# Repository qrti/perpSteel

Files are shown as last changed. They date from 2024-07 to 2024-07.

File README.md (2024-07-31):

# **Perpetual Steel Ball Track**

### As perpetual as the laws of physics of this universe allow
<br>

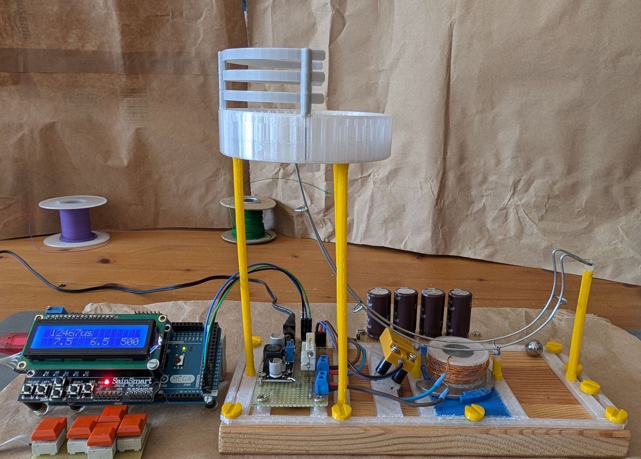
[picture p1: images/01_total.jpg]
<br>

YouTube Video  
https://www.youtube.com/watch?v=C1I4kvoMqeI

[**-> views**](#views)  
[**-> source**](source)  
<br>

## Background
The idea for building this device came to me while looking at a commercially available version. It was a long journey with much trial and error before the replica finally worked. The track had to be bent from steel wire, parts for the frame, collecting bowl, and supports had to be made with the 3D printer, the electromagnet had to be wound, and the electronics and software had to be developed
<br>

## Build
The building instructions for this project are not complete, they are only intended as an aid for a replica  
[**-> 3D-Printed Parts**](stl)

**Inner and Outer Track Template**  
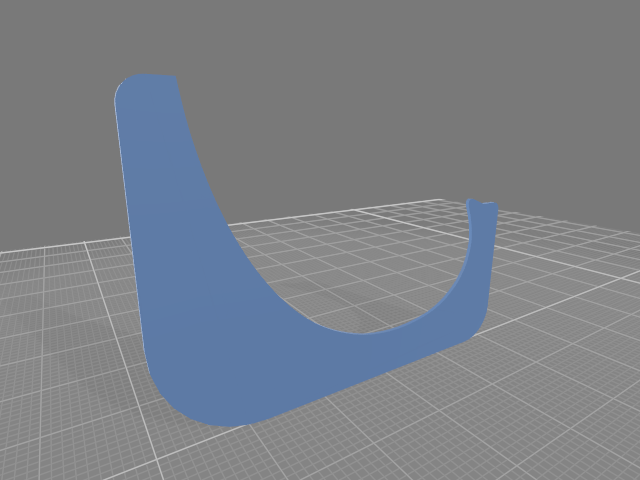
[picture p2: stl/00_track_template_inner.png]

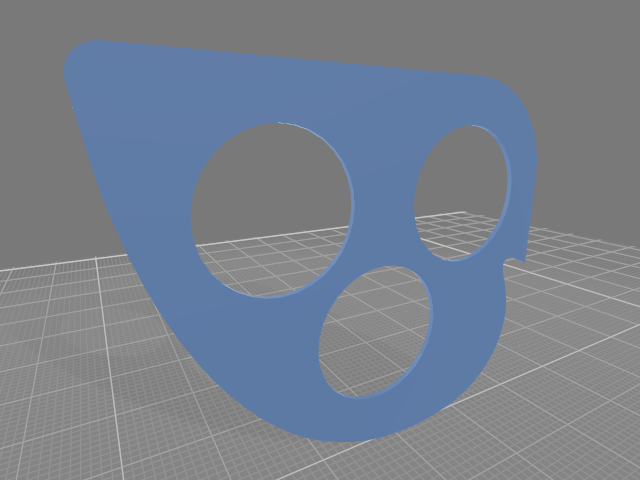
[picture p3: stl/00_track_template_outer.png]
  
The track was bent from 1.5 mm galvanized iron wire, as this is easy to work with and solder,  
the templates are meant to make bending easier  
<br>

**Cup and Cup Guide**  
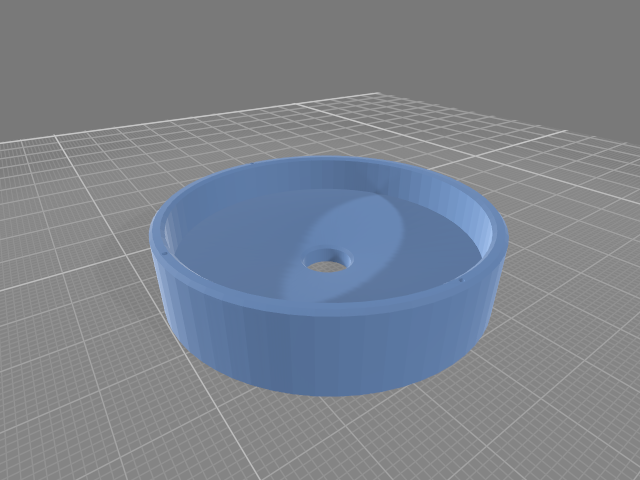
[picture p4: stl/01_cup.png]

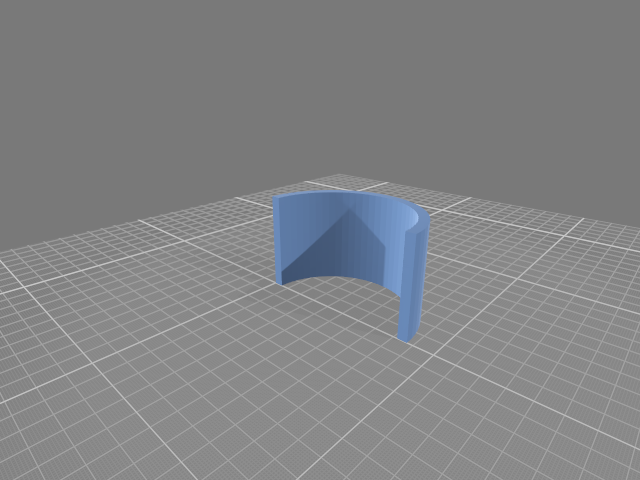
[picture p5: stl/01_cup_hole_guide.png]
  
To prevent the steel ball from derailing a guide is glued to the outlet of the cup hole  
<br>

**Rail Type 1 and 2**  
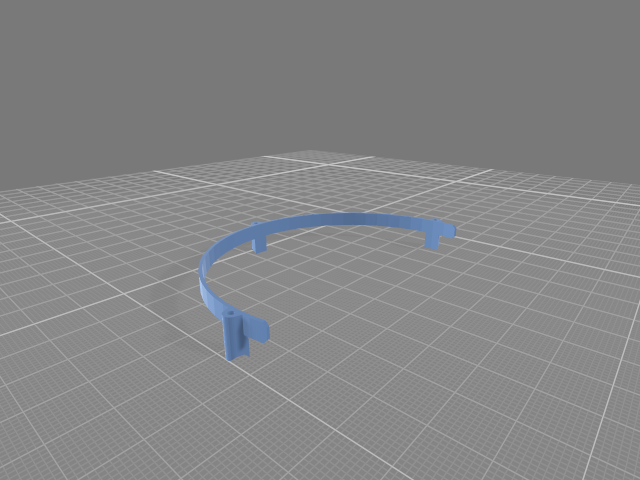
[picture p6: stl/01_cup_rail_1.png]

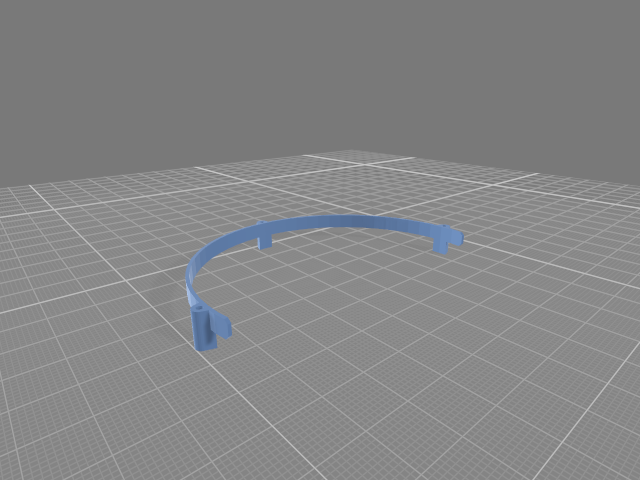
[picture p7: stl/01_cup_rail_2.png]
  
Type 1 is fixed to the rim of the cup, two pieces of type 2 are mounted above,  
to connect cup and rails sticks of steel wire are put in the provided holes  
<br>

**Electro Magnet Bobbin and Magnetic Field Guide Template**  
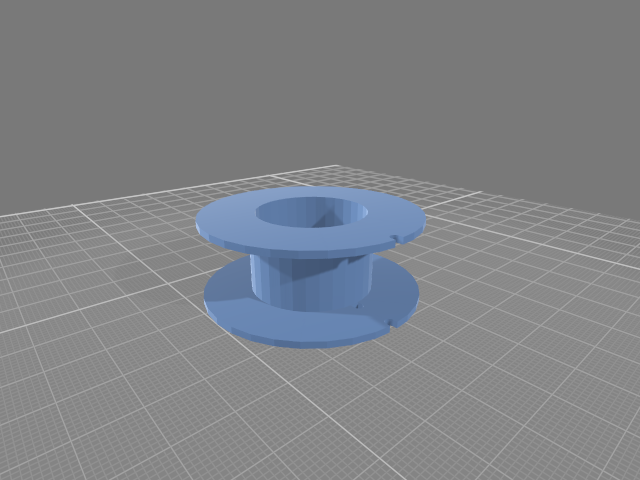
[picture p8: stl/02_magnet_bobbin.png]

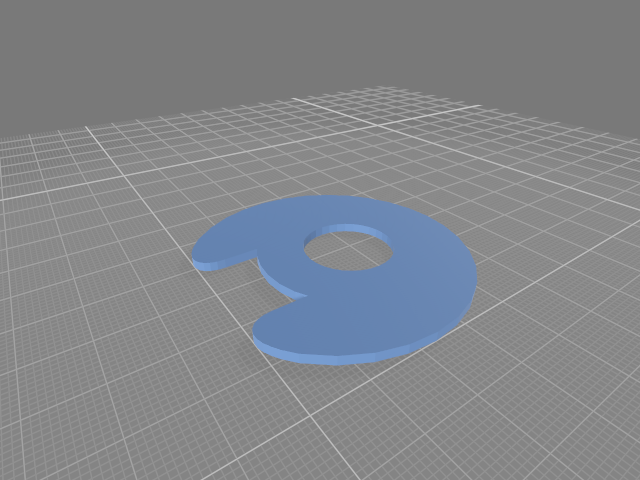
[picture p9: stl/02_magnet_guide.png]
  
The bobbin is completely wound with 0.8 mm enameled copper wire,  
the soft iron core has a diameter of 20 mm and is 16 mm long,  
the magnetic field guide is intended to center the steel ball in front of the magnet,  
it is made from 3 mm thick sheet iron, only the outlines of the template are relevant,  
so the hole in the template is not transferred to the sheet  
(the field guide can possibly be omitted)  
<br>

**Inductive Proximity Sensor and Arduino**  
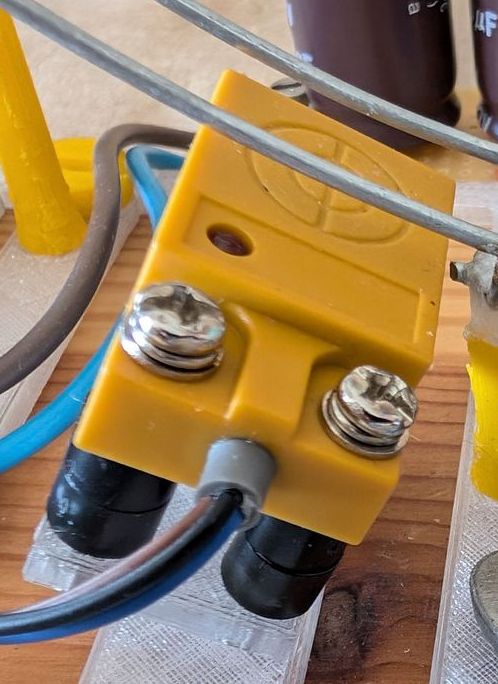
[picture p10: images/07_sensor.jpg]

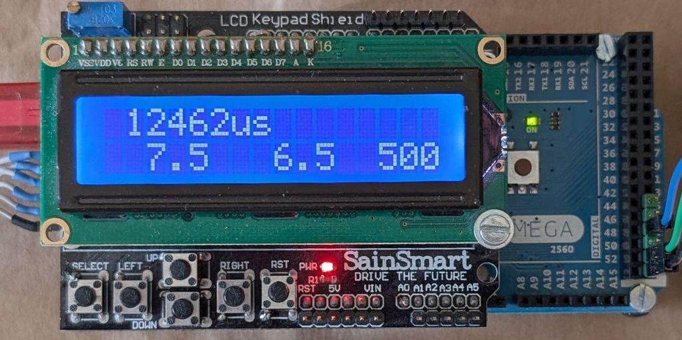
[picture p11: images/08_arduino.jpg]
  
This kind of sensor is normally used in 3D-Printers, see the schematic for more details,  
an Arduino Mega 2560 handles timing and delays for sensor and magnet,  
the LCD shows current settings, the keys allow timing changes  
<br>

## Schematic
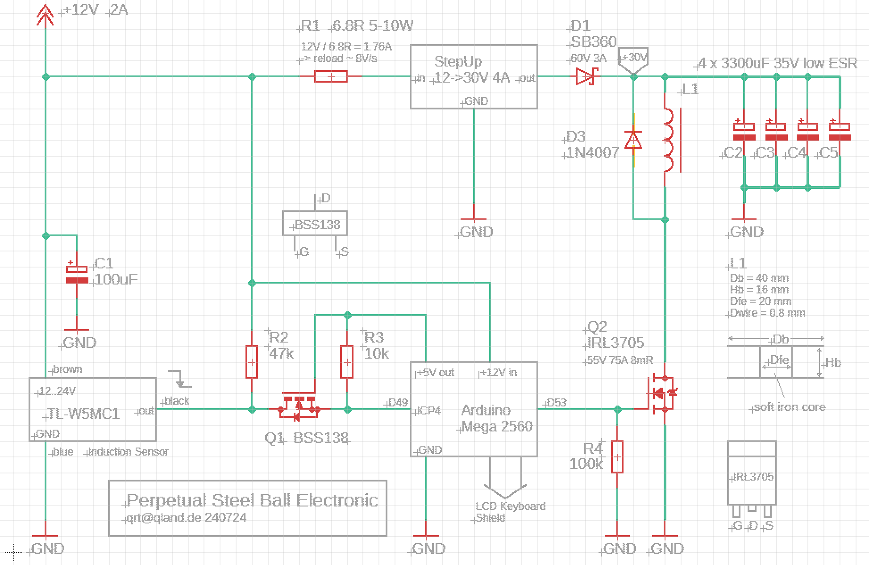
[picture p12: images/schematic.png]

<br>

## Operation
**Right Key**  
press about 1.5 s to enter or exit time and delay settings

**Select Key**  
change values in 100 / 500 / 1000 ms steps

**Left Key - / Right Key +**  
sensor OFF -> magnet ON delay

**Down Key - / Up Key +**  
magnet ON time  

(timing is saved to EEPROM after changes)

**Display**  
*Line 1*  
status or averaged sensor ON to OFF time in us

*Line 2*  
sensor OFF -> magnet ON delay in ms  
magnet ON time in ms  
change value in ms

**Calculation**  
sensor ON to OFF time is measured in TIMER4_CAPT and used as reciprocal relative speed (Vr)  
Vr is averaged and weighted, it influences the sensor OFF -> magnet ON delay
<br>

<br>
<br>

**Inspired by**  
https://www.youtube.com/watch?v=r_LG8FDt51U&t

**How to make a Steel Marble Track**  
https://www.youtube.com/watch?v=kPguktA674w

**Code Edited and Developed with**  
https://code.visualstudio.com/  
https://platformio.org/

<br>

---

<br>

## Views

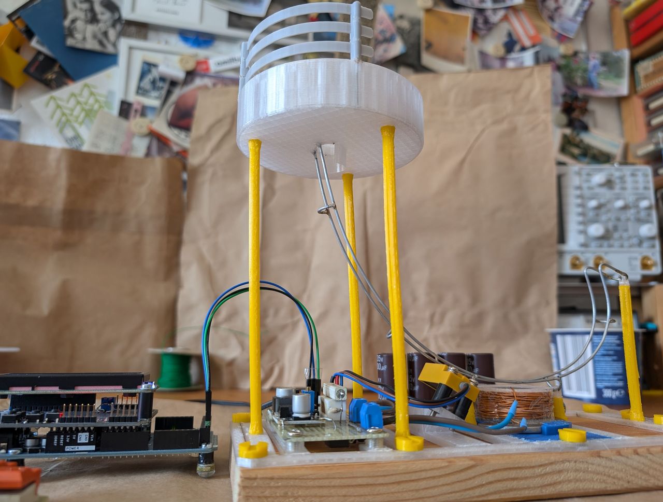
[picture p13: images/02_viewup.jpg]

<br>
<br>

Stepup Electronic and Capacitor Charge Resistors  
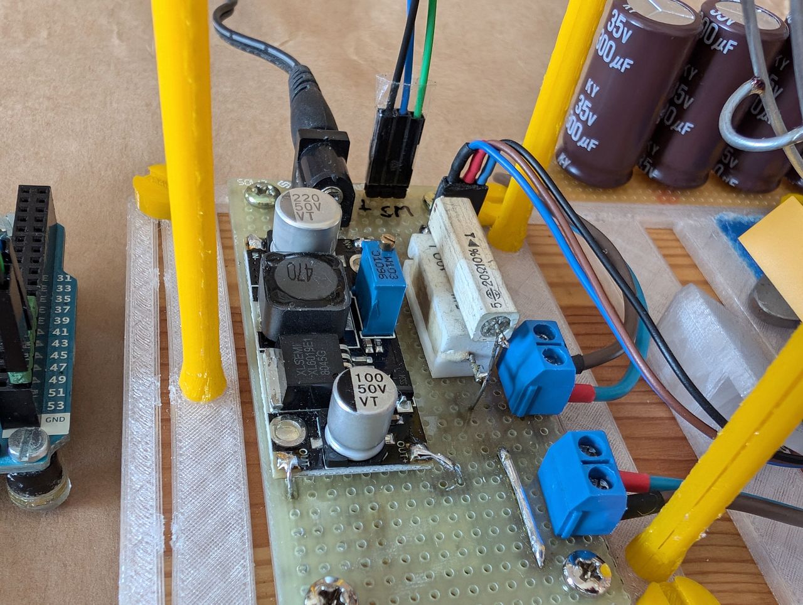
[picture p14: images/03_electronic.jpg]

<br>
<br>

Low ESR Capacitors 4 x 3300uF 35V  
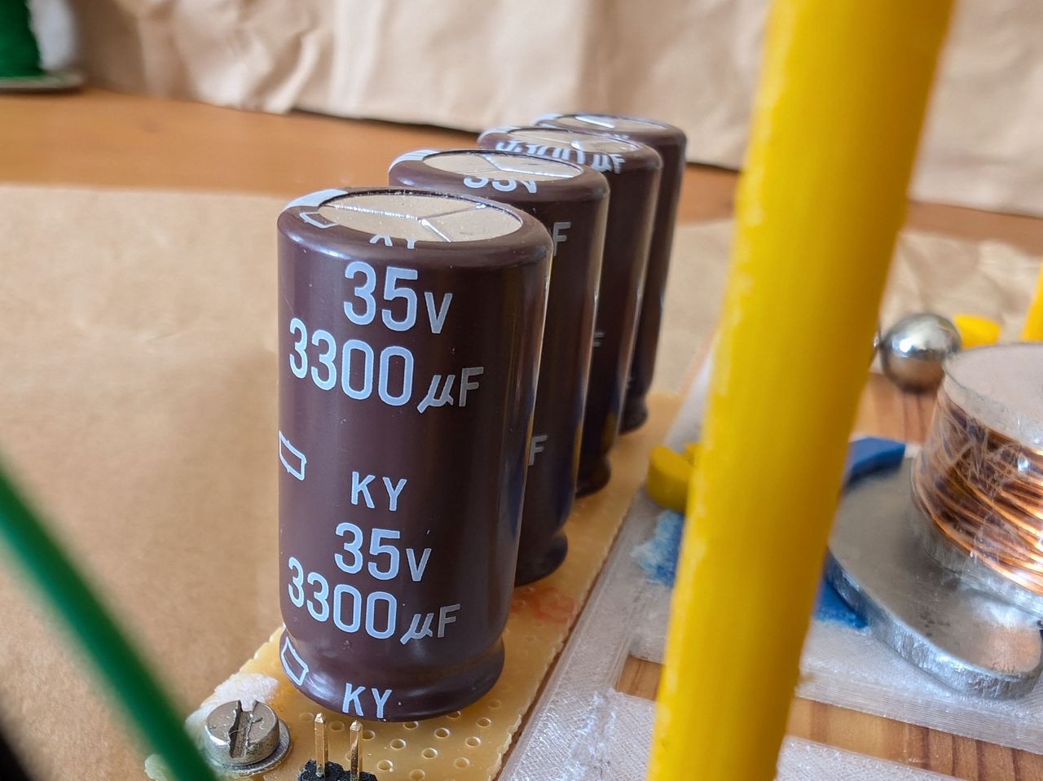
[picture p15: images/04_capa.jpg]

<br>
<br>

Inductive Proximity Sensor and Electro Magnet on Top of Magnetic Field Guide  
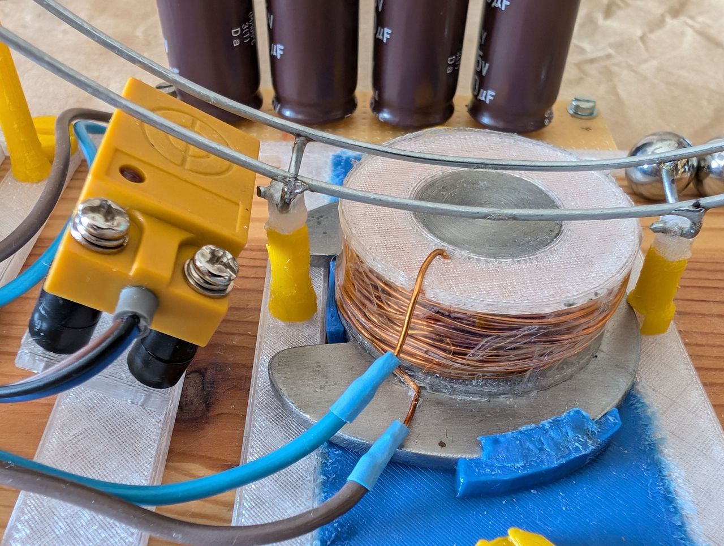
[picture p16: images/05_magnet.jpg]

<br>
<br>

Arduino Mega 2560 with LCD and Key Shield  
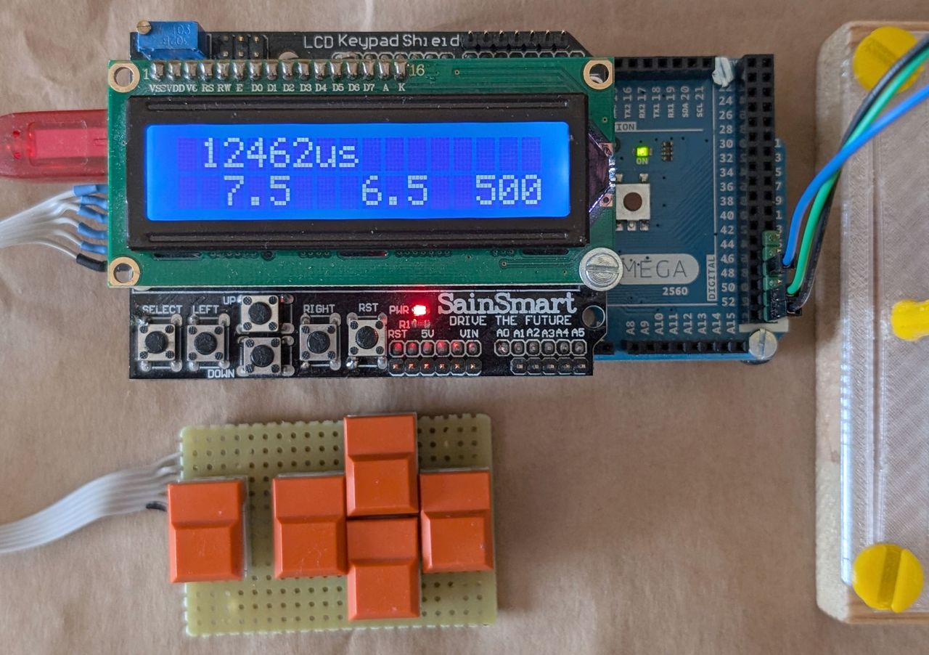
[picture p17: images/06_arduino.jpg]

<br>
<br>

<br>
<br>

---

[qrt@qland.de](mailto:qrt@qland.de) 240731

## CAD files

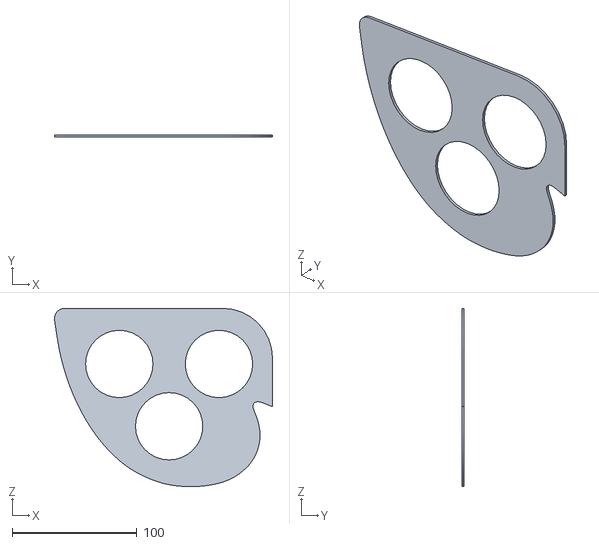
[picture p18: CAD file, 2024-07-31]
stl/00_track_template_outer.stl
174.9 x 2.00 x 143.2

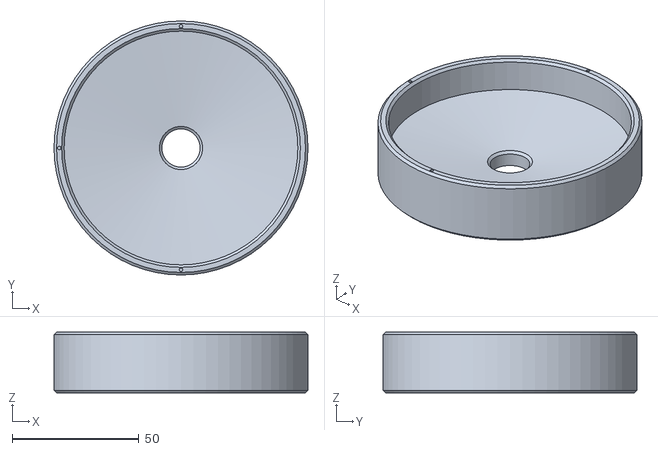
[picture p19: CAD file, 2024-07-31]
stl/01_cup.stl
100.0 x 100.0 x 24.0

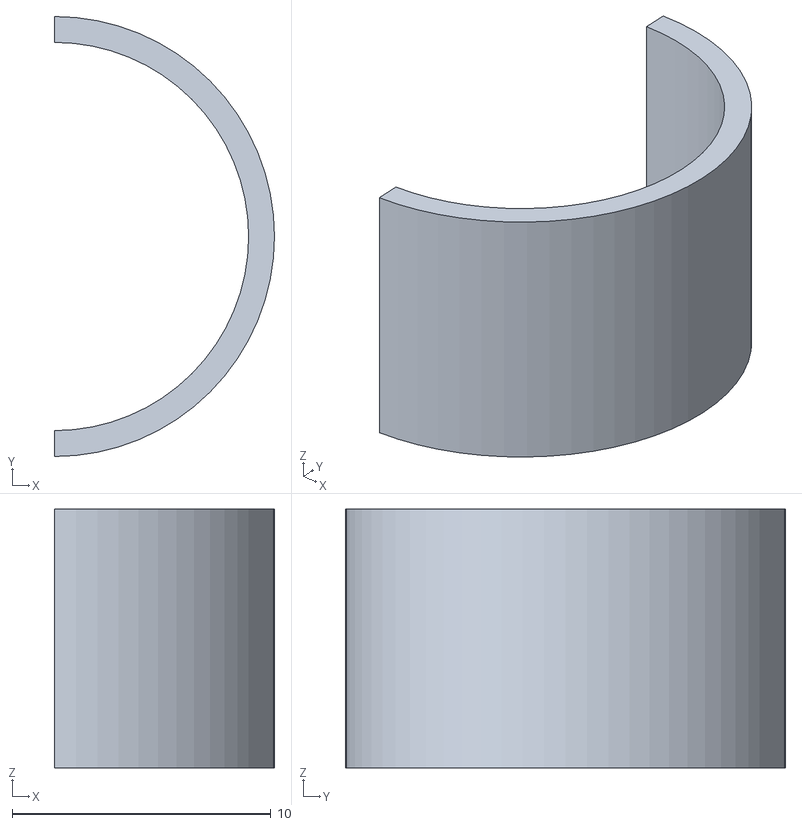
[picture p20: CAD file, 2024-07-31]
stl/01_cup_hole_guide.stl
8.50 x 17.0 x 10.0

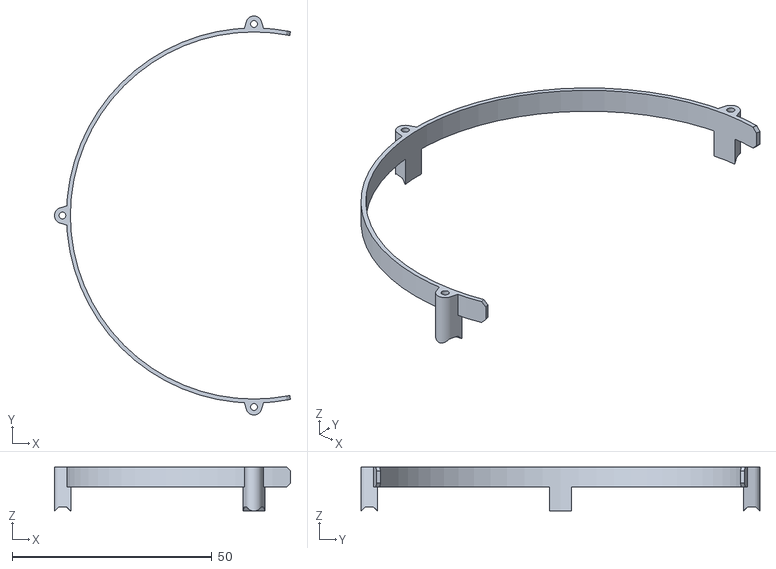
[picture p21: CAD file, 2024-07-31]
stl/01_cup_rail_1.stl
59.2 x 100.0 x 11.0

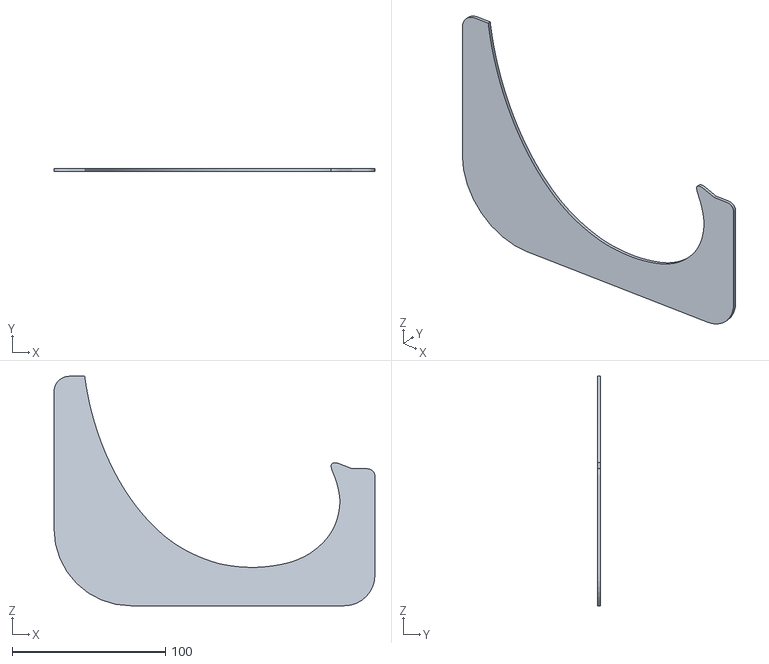
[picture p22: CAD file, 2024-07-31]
stl/00_track_template_inner.stl
209.3 x 2.00 x 149.7

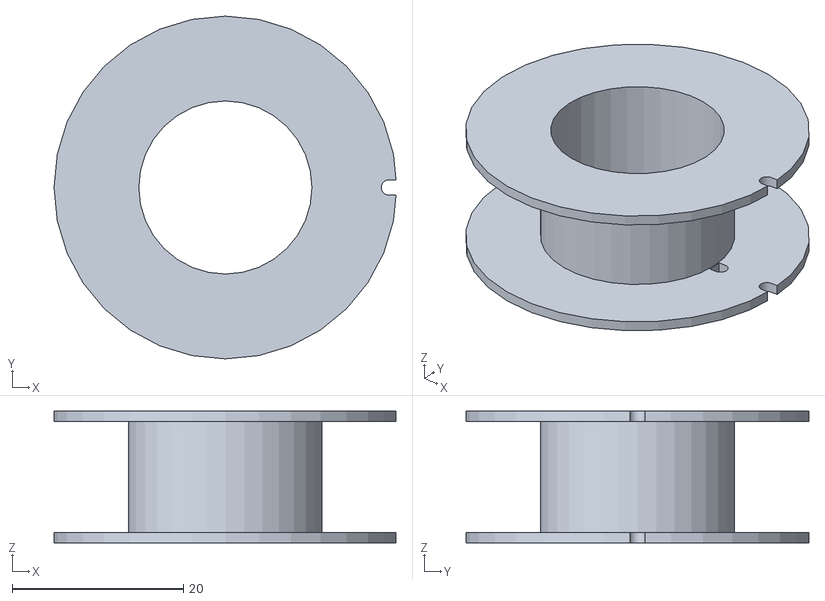
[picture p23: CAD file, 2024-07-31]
stl/02_magnet_bobbin.stl
39.9 x 40.0 x 15.4

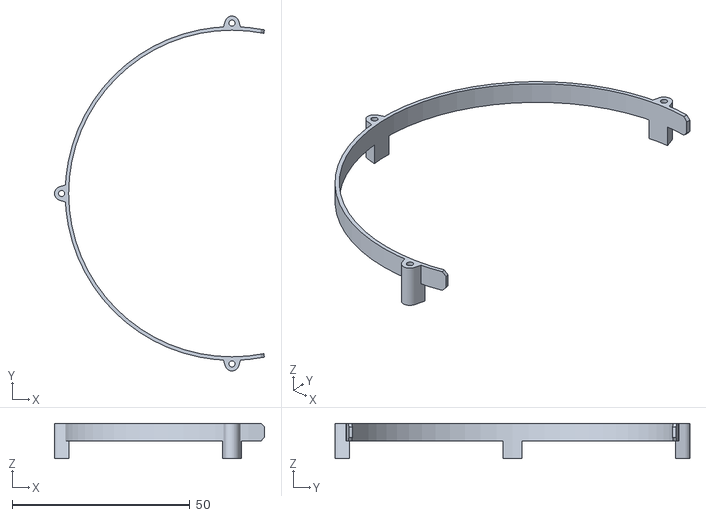
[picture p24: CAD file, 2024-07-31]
stl/01_cup_rail_2.stl
59.2 x 100.0 x 10.0

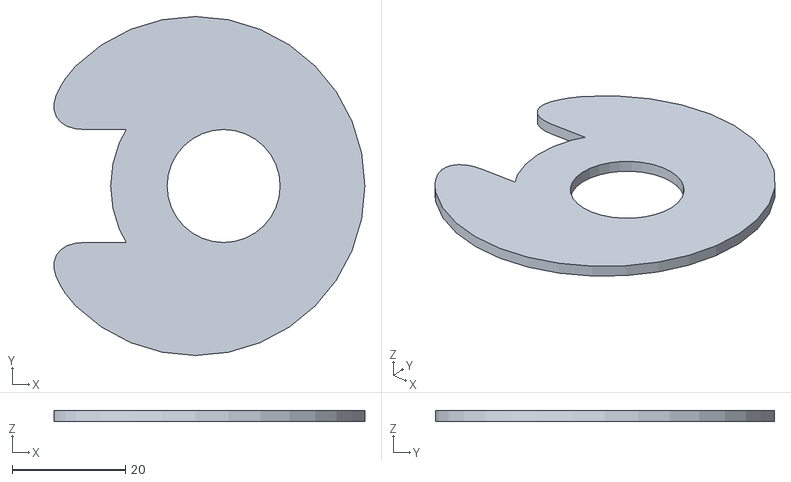
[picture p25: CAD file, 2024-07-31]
stl/02_magnet_guide.stl
55.0 x 60.0 x 2.00

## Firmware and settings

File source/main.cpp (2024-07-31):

// perpSteel V0.4, qrt@qland.de 240731

// KEY_RIGHT 
// press > 1.5 s to enter or exit time and delay settings
//
// KEY_SELECT
// change values in 100..500..1000 ms steps
//
// KEY_LEFT - / KEY_RIGHT +
// delay sensor OFF -> magnet ON
// 
// KEY_DOWN - / KEY_UP +
// magnet ON time
//
// the timing is saved to EEPROM after changes

// display
// line 1: status
//      2: sensor OFF -> magnet ON delay in ms, magnet ON time in ms, change value in ms

// calculation
// sensor ON to OFF time is measured in TIMER4_CAPT and used as reciprocal relative speed (Vr)
// Vr is averaged and weighted, it influences the sensor OFF -> magnet ON delay

// possible ICP pins on Arduino Mega 2560
// PIN      PORT    ICP     DIGITAL PIN     TIMER
// 35	    PL0     4       49              4
// 36	    PL1     5	    48              5

#include <Arduino.h>
#include <LiquidCrystal.h>
#include <EEPROM.h>
#include "LCDKeypadDA.h"

// default values for this machine, might be different for other machines
#define DEFAULT_TDELAY       6800               // sensor OUT -> magent ON delay    in us   
#define DEFAULT_TMAGPO       6000               // magnet ON time
#define DEFAULT_TNAVG       11000               // sensor ON to OFF time (Vr)

#define EESIG          0x18ab11cd               // EEPROM unique ID   

void changePars();

void showTiming();
void saveTiming();
void loadTiming();

void init_tmr4();

LiquidCrystal lcd(8, 9, 4, 5, 6, 7);
LCDKeypad keypad;

const int PIN_LED = 13;                         // LED
const int PIN_KEY_IRQ = 2;                      // IRQ0 for keys

const int PIN_INDUCT_SENSE = 49;                // ICP 4, TIMER 4
const int PIN_MAGPOW = 53;                      // magnet power 

#define ON      HIGH
#define OFF     LOW

volatile int32_t tdelay, tmagpo, dt;           // in us
uint32_t tdelayC;

volatile int32_t tsense;
volatile uint8_t f_capture = 0;                // flag

char buf[32];
int32_t tnSum, tnAvg, tnAvc=16;

// - - - - - - - - - - - - - - - - - - - - - - - - - - - - - - - - - - - - - - -

void setup()
{
    lcd.begin(16, 2);   
    lcd.clear();

    lcd.setCursor(0, 0);
    lcd.print("qrt 240731");

    pinMode(PIN_LED, OUTPUT);
    digitalWrite(PIN_LED, OFF);

    pinMode(PIN_INDUCT_SENSE, INPUT);

    pinMode(PIN_MAGPOW, OUTPUT);
    digitalWrite(PIN_MAGPOW, OFF);

    pinMode(A0, INPUT);

    loadTiming();

    delay(1000);
    lcd.clear();
    showTiming();

    init_tmr4();    
}

// - - - - - - - - - - - - - - - - - - - - - - - - - - - - - - - - - - - - - - -

uint32_t tmD, tmM;

void loop() 
{
    lcd.setCursor(0, 0);
    sprintf(buf, "%6luus   ", tnAvg);
    lcd.print(buf);

    tmD = tmagpo / 1000;
    tmM = tmagpo % 1000;

    f_capture = 0;

    while(!f_capture && !keypad.digPress())
        ;

    if(keypad.digPress())
        changePars();

    if(!(TIFR4 & 1<<TOV4)){
        tdelayC = tdelay + (tsense - tnAvg) * tdelay / tnAvg;

        delay(tdelayC / 1000);
        delayMicroseconds(tdelayC % 1000);
        digitalWrite(PIN_MAGPOW, ON);

        delay(tmD);
        delayMicroseconds(tmM);
        digitalWrite(PIN_MAGPOW, OFF);

        tnSum += tsense - tnAvg;
        tnAvg = tnSum / tnAvc;        

        lcd.setCursor(0, 0);
        lcd.print("wait ...");
    }
    // else{
    //     lcd.setCursor(0, 0);
    //     lcd.print("fail    ");       
    // }

    delay(100);
}

// - - - - - - - - - - - - - - - - - - - - - - - - - - - - - - - - - - - - - - -

void init_tmr4()
{  
    TCCR4A = 0;                                         // reset timer registers
    TCCR4B = 0;                                         //

    TCCR4B = 1<<ICNC4 | 0<<ICES4 | 1<<CS41;             // input noise canceler on, input capture negative edge, start T4 prescaler 8 (2 MHz)
    TIMSK4 = 1<<ICIE4;                                  // input capture IR enable 
}

ISR(TIMER4_CAPT_vect)
{
    if(TCCR4B & 1<<ICES4){                              // positive edge
        tsense = ICR4 >> 1;                             // low period in us
        TCCR4B = 1<<ICNC4 | 0<<ICES4 | 1<<CS41;         // negative edge next 
        f_capture = 1;                                  // flag capture
    }
    else{                                               // negative edge
        TCNT4 = 0;                                      // reset T4 counter
        TCCR4B = 1<<ICNC4 | 1<<ICES4 | 1<<CS41;         // positive edge next
        TIFR4 |= 1<<TOV4;                               // reset T4 OV IR
    }
}

// - - - - - - - - - - - - - - - - - - - - - - - - - - - - - - - - - - - - - - -

void changePars()
{
    uint8_t pc = 0;                                     // 10 ms press counter

    while(keypad.digPress() && pc<KEYLONG){             // wait for key long press
        pc++;                                           //
        delay(10);                                      //
    }                                                   //                      

    if(pc < 150)                                        // if press was too short
        return;                                         // return

    lcd.setCursor(0, 0);                                // display message
    lcd.print("edit timing");                           //

    while(keypad.digPress())                            // wait until key is released
        delay(10);                                      //

    delay(250);                                         // debounce delay 

// - - - - - - - - - - - - - - - - - - -

    int8_t key=KEY_NONE, ckey;                          // key variables    
    uint8_t rc = 0;                                     // 10 ms release counter
    pc = 0;                                             //       press

    while(true){                                        // loop start
        ckey = keypad.getKey();                         // get current key

        if(ckey != KEY_NONE){                           // key pressed
            key = ckey;                                 // store key
            rc = 0;                                     // reset release counter
            if(pc < 255) pc++;                          // advance and restrict press counter
        }
        else{
            if(pc > 5){                                 // key released, min press time
                if(key == KEY_LEFT){
                    tdelay -= dt;
                    if(tdelay < 0) tdelay = 0;
                }
                else if(key == KEY_RIGHT){
                    tdelay += dt;
                }
                else if(key == KEY_DOWN){
                    tmagpo -= dt;
                    if(tmagpo < 0) tmagpo = 0;
                }
                else if(key == KEY_UP){
                    tmagpo += dt;
                }
                else if(key == KEY_SELECT){
                    if(dt == 100)   
                        dt = 500;
                    else if(dt == 500)
                        dt = 1000;
                    else if(dt == 1000)
                        dt = 100;
                }

                showTiming();
            }
            
            key = KEY_NONE;
            pc = 0;                                     // reset press counter
            if(rc < 255) rc++;                          // advance and restrict release counter
        }

        if(ckey==KEY_RIGHT && pc>KEYLONG)               // if key right long press
            break;                                      // exit loop

        delay(10);
    }

    lcd.setCursor(0, 0);                                // clear display
    lcd.print("save timing");                           //

    while(keypad.digPress())                            // wait until key is released
        delay(10);                                      //

    delay(250);                                         // debounce delay 

    saveTiming();                                       // save timing
}

// - - - - - - - - - - - - - - - - - - - - - - - - - - - - - - - - - - - - - - -

void showTiming()
{
    static char bufi[32];

    dtostrf((float)tdelay/1000., 5, 1, bufi);                 // float number, min width, precision, target string
    strcat(bufi, " ");
    dtostrf((float)tmagpo/1000., 5, 1, &bufi[strlen(bufi)]);   
    strcat(bufi, " ");
    dtostrf((float)dt, 4, 0, &bufi[strlen(bufi)]);  
    strcat(bufi, " ");

    lcd.setCursor(0, 1);
    lcd.print(bufi);
}

// - - - - - - - - - - - - - - - - - - - - - - - - - - - - - - - - - - - - - - -

int eead;

void eePut(uint32_t v)
{
    EEPROM.put(eead, v);
    eead += sizeof(int32_t);
}

void saveTiming()
{   
    eead = 0;

    eePut(EESIG);
    eePut(tdelay);
    eePut(tmagpo);
    eePut(dt);
    eePut(tnAvg);
}

uint32_t eeGet()
{
    uint32_t v;

    EEPROM.get(eead, v);
    eead += sizeof(int32_t);
    return v;
}

void loadTiming()
{
    eead = 0;

    if(eeGet() == EESIG){
        tdelay = eeGet();
        tmagpo = eeGet();
        dt = eeGet();
        tnAvg = eeGet();
    }
    else{
        tdelay = DEFAULT_TDELAY;
        tmagpo = DEFAULT_TMAGPO;
        tnAvg = DEFAULT_TNAVG;
        dt = 500;            
    }
    
    tnSum = tnAvg * tnAvc;  
}

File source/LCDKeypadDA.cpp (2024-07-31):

#include "LCDKeypadDA.h"

#include "Arduino.h"

uint16_t keyVals[NUMKEYS] = { 30, 150, 360, 535, 760 };           // official values

LCDKeypad::LCDKeypad()            
{
    pinMode(KEYPIN, INPUT);
}

// digital press check, senses KEY_RIGHT only
//
bool LCDKeypad::digPress()
{
    return digitalRead(KEYPIN) == 0;
}

// analog get key
//
int8_t LCDKeypad::getKey()
{
    uint16_t ad = analogRead(KEYPIN);
    int8_t k;
    
    for(k=0; k<NUMKEYS; k++)
        if(ad < keyVals[k])
            break;

    if(k == NUMKEYS)
        k = KEY_NONE;
        
    return k;    
}

bool LCDKeypad::keyPressed(int key){
    
    return getKey() == key;
}

void LCDKeypad::waitKeyRelease()
{
    while(analogRead(KEYPIN) < ADNOKEY)
        ;
}
